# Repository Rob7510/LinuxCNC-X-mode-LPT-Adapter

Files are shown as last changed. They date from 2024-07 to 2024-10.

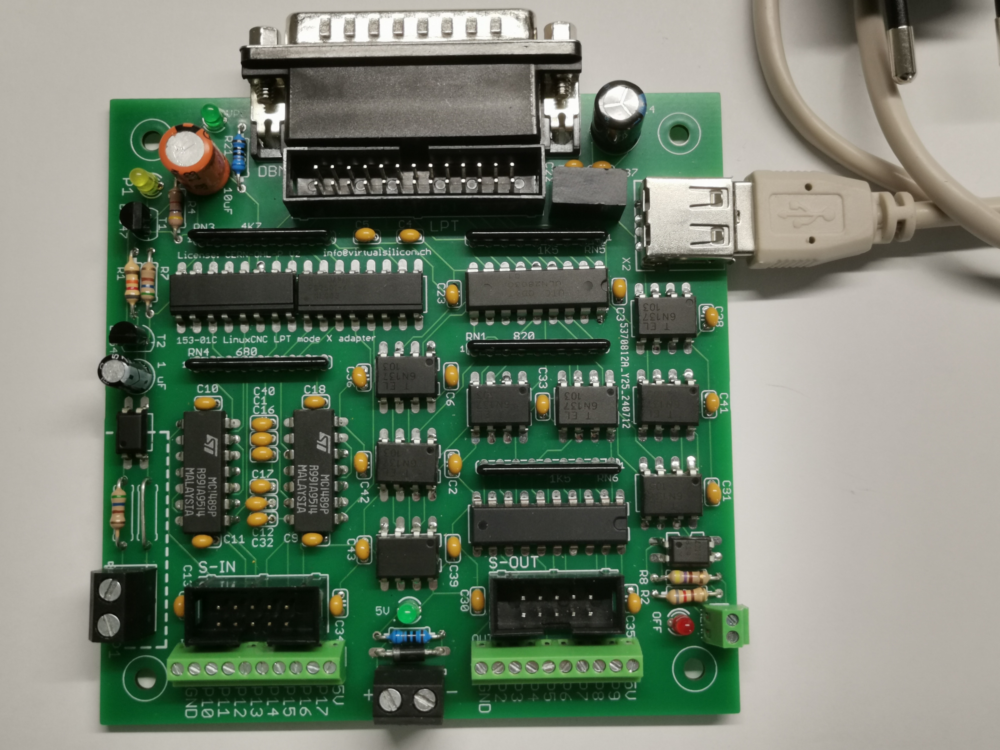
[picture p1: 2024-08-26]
153-01C LPT-X mode adapter prototype.jpg

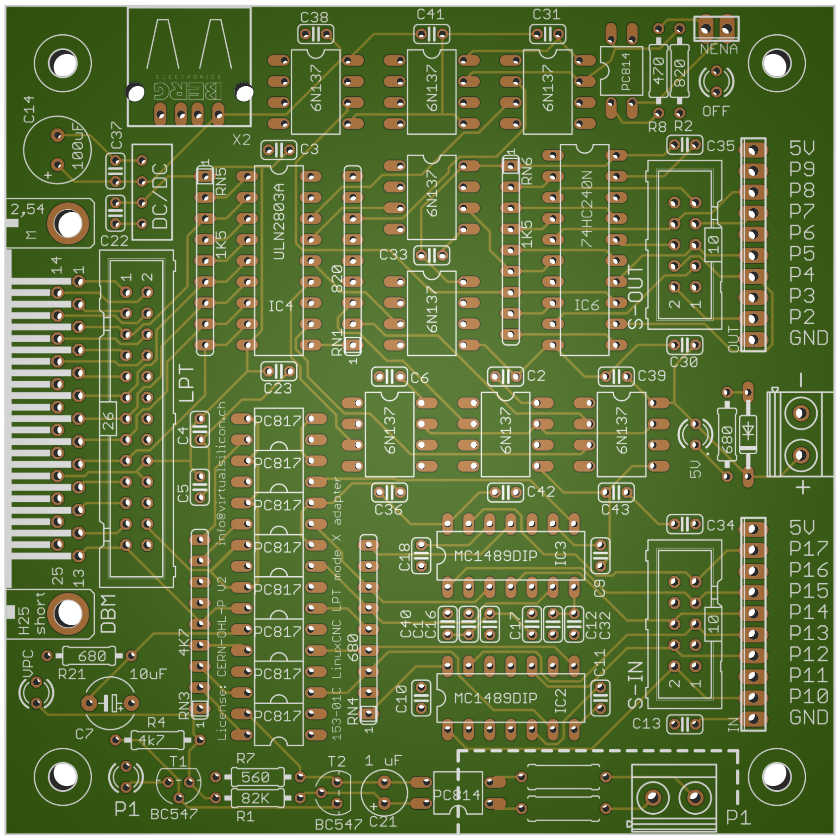
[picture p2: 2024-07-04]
153-01C image.png

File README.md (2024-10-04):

# LinuxCNC signal adapter for a parallel port operating in X-mode.
**Version 153-01C**

Many PC printer port option boards can be operated in 'X' mode in **LinuxCNC**, by setting this mode in the 'loadrt hal_parport' command.
In X-mode the 25-pin I/O connector provides 9 input ports (Pin 1, Pin 10-17) and 8 output ports (Pin 2 - Pin 9). This is usually sufficient for a small CNC. (I do not know if other software than LinuxCNC can set a Printer port card in X-mode).

The signal breakout for an X-mode adapter can be home built with a low cost dual layer PCB, with full electric isolation from the connected PC. This document provides the Eagle design and the Gerber manufacturing files for such a Breakout Board (BoB). The board size is kept to 10 x 10 cm to keep the manufacturing costs low (with Far-East PCB services). The **CERN-OHL-P V2** OpenHardware license applies, hence you are free to copy the design, modify it and sell/use the result.

**Design:**

  * The BoB input and output ports are electrically separated from the PC using optical couplers. The PC side of the circuit is powered via a small 5V isolated DC/DC converter. Te board uses approximately 150 mA, and can be powered with an old USB-A power adapter.
  * The board can be directly plugged into a 25 pin PC printer port, or connected via a standard 26 wire ribbon cable with a printer port connector on the other end. The 26 pin connector can also be used to plug in a signal monitor.
  * The Inputs for Pins 10 through 17 support a wide range of input signals (<u>+</u> 30V). The Pin 1 Input is fully isolated from the whole board, and can handle up to 300V AC or DC signals, for instance to check presence of the mains voltage or Power supply output.

**Inputs:**

**Pin 1** requires one or two series resistors (for DC) or capacitors (for AC) so that the current through the bipolar optocoupler (PC814) is in the range of 4 - 10 mA:
* For standard 5V signals use a 680 Ohm resistor. For voltages over 100V use two components in series.
* For DC voltages make sure the power dissipation in the resistor(s) does not exceed their rating.
* For 230V mains voltage use 2 x 150nF (400V) in series. To keep high voltages away from the board, mount the capacitors or resistors at the source, and fill the two onboard slots with jumpers.
* The P1 LED lights up when it detects a valid signal.

**Pins 10 - 17** are set to about 0V (False) for an input between -30 and + 0.5 V, and to 5V (True) for an input between 1.5 an 30V. These inputs suppress high frequency (>5KHz) pulses. The 10 pin ribbon connector connects Pin 10 - 17, as well as GND and 5V to a remote input panel.

**Outputs:**

**Pins 2 - 9 ** drive 5V signals with a current up to 35 mA. The fast optical couplers (6N137) can handle pulses as short as 2 microseconds. The 10 pin ribbon connector is for connection to a remote breakout panel. All outputs (typically used for stepper signals) can be collectively turned off with a logic input signal.

**Power supply:**

The USB connector on the BoB should be connected to an separate 5V USB power supply to maintain electric isolation from the PC. The onboard 2-pin 5V connector can be used to supply other 5V hardware like relay boards. If PC isolation is not needed, the BoB can be connected to one of the PC USB plugs, and the DC/DC converter can be replaced by two wires.

**Software:** XPtest-0.hal and xptest-0.xml provide a display of the X-mode adapter I/O ports and check / set their status. The test assumes that the BoB connects to the first printer port that the PC discovers.

**Assembly:**

The X-mode adapter 153-01C uses through-hole components to facilitate home assembly. The component list (BOM) has the details.
The small capacitors (useful values between 10 and 100 nF) are required to suppress RF disturbance.
The antiparallel diode next to the power connector will prevent damage in case the 5V is connected with the wrong polarity (I hate replacing dead chips).

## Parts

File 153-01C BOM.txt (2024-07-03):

Stückliste exportiert aus /home/robert/Project_data/Projects/153 LinuxCNC adapters/153-01C Mode X LPT adapter.sch am 03/07/2024 21:08

Part     Value     Device          Package         Description                           MF MPN          OC_FARNELL OC_NEWARK
.                  LED3MM          LED3MM          LED                                                                       
5V                 MKDSN1,5/2-5,08 MKDSN1,5/2-5,08 MKDSN 1,5/ 2-5,08 Printklemme                                             
AC/DC-IN           MKDSN1,5/2-5,08 MKDSN1,5/2-5,08 MKDSN 1,5/ 2-5,08 Printklemme                                             
C1                 C-EU025-024X044 C025-024X044    CAPACITOR, European symbol                                                
C2                 C-EU025-024X044 C025-024X044    CAPACITOR, European symbol                                                
C3                 C-EU025-024X044 C025-024X044    CAPACITOR, European symbol                                                
C4                 C-EU025-024X044 C025-024X044    CAPACITOR, European symbol                                                
C5                 C-EU025-024X044 C025-024X044    CAPACITOR, European symbol                                                
C6                 C-EU025-024X044 C025-024X044    CAPACITOR, European symbol                                                
C7       10uF      CPOL-EUE5-6     E5-6            POLARIZED CAPACITOR, European symbol                                      
C9                 C-EU025-024X044 C025-024X044    CAPACITOR, European symbol                                                
C10                C-EU025-024X044 C025-024X044    CAPACITOR, European symbol                                                
C11                C-EU025-024X044 C025-024X044    CAPACITOR, European symbol                                                
C12                C-EU025-024X044 C025-024X044    CAPACITOR, European symbol                                                
C13                C-EU025-024X044 C025-024X044    CAPACITOR, European symbol                                                
C14      100uF     CPOL-EUE3.5-8   E3,5-8          POLARIZED CAPACITOR, European symbol                                      
C16                C-EU025-024X044 C025-024X044    CAPACITOR, European symbol                                                
C17                C-EU025-024X044 C025-024X044    CAPACITOR, European symbol                                                
C18                C-EU025-024X044 C025-024X044    CAPACITOR, European symbol                                                
C21      1 uF      CPOL-EUE2.5-6   E2,5-6          POLARIZED CAPACITOR, European symbol                                      
C22                C-EU025-024X044 C025-024X044    CAPACITOR, European symbol                                                
C23                C-EU025-024X044 C025-024X044    CAPACITOR, European symbol                                                
C30                C-EU025-024X044 C025-024X044    CAPACITOR, European symbol                                                
C31                C-EU025-024X044 C025-024X044    CAPACITOR, European symbol                                                
C32                C-EU025-024X044 C025-024X044    CAPACITOR, European symbol                                                
C33                C-EU025-024X044 C025-024X044    CAPACITOR, European symbol                                                
C34                C-EU025-024X044 C025-024X044    CAPACITOR, European symbol                                                
C35                C-EU025-024X044 C025-024X044    CAPACITOR, European symbol                                                
C36                C-EU025-024X044 C025-024X044    CAPACITOR, European symbol                                                
C37                C-EU025-024X044 C025-024X044    CAPACITOR, European symbol                                                
C38                C-EU025-024X044 C025-024X044    CAPACITOR, European symbol                                                
C39                C-EU025-024X044 C025-024X044    CAPACITOR, European symbol                                                
C40                C-EU025-024X044 C025-024X044    CAPACITOR, European symbol                                                
C41                C-EU025-024X044 C025-024X044    CAPACITOR, European symbol                                                
C42                C-EU025-024X044 C025-024X044    CAPACITOR, European symbol                                                
C43                C-EU025-024X044 C025-024X044    CAPACITOR, European symbol                                                
D1                 1N4148DO35-10   DO35-10         DIODE                                                                     
DBM                M25HP           M25HP           SUB-D                                                 unknown    unknown  
DC/DC              VA-1205S        4SIL            DC DC Converter Single Output, 1 Watt                 unknown    unknown  
IC2      MC1489DIP MC1489DIP       DIL14           MC1489 quad line receiver DIP14                                           
IC3      MC1489DIP MC1489DIP       DIL14           MC1489 quad line receiver DIP14                                           
IC4      ULN2803A  ULN2803A        DIL18           DRIVER ARRAY                                                              
IC6      74HC240N  74HC240N        DIL20           Octal BUFFER and LINE DRIVER, 3-state                                     
IN                 MPT10           10POL254        PHOENIX CONNECTOR                                     unknown    unknown  
LPT                ML26            ML26            HARTING                                               unknown    unknown  
NENA               MPT2            2POL254         PHOENIX CONNECTOR                                     unknown    unknown  
OFF                LED3MM          LED3MM          LED                                                                       
OK-SIG   PC814     PC814           DIL04           SHARP OPTO COUPLER                                    9707662    unknown  
OK-SIG1  PC814     PC814           DIL04           SHARP OPTO COUPLER                                    9707662    unknown  
OK10     PC817     PC817           DIL04           SHARP OPTO COUPLER                       PC817X4J000F 9707727    97K7059  
OK11     PC817     PC817           DIL04           SHARP OPTO COUPLER                       PC817X4J000F 9707727    97K7059  
OK12     PC817     PC817           DIL04           SHARP OPTO COUPLER                       PC817X4J000F 9707727    97K7059  
OK13     PC817     PC817           DIL04           SHARP OPTO COUPLER                       PC817X4J000F 9707727    97K7059  
OK14     PC817     PC817           DIL04           SHARP OPTO COUPLER                       PC817X4J000F 9707727    97K7059  
OK15     PC817     PC817           DIL04           SHARP OPTO COUPLER                       PC817X4J000F 9707727    97K7059  
OK16     PC817     PC817           DIL04           SHARP OPTO COUPLER                       PC817X4J000F 9707727    97K7059  
OK17     PC817     PC817           DIL04           SHARP OPTO COUPLER                       PC817X4J000F 9707727    97K7059  
OKP2     6N137     6N137           DIL08           MOTOROLA OPTO COUPLER                    6N137        1328376    52M1895  
OKP3     6N137     6N137           DIL08           MOTOROLA OPTO COUPLER                    6N137        1328376    52M1895  
OKP4     6N137     6N137           DIL08           MOTOROLA OPTO COUPLER                    6N137        1328376    52M1895  
OKP5     6N137     6N137           DIL08           MOTOROLA OPTO COUPLER                    6N137        1328376    52M1895  
OKP6     6N137     6N137           DIL08           MOTOROLA OPTO COUPLER                    6N137        1328376    52M1895  
OKP7     6N137     6N137           DIL08           MOTOROLA OPTO COUPLER                    6N137        1328376    52M1895  
OKP8     6N137     6N137           DIL08           MOTOROLA OPTO COUPLER                    6N137        1328376    52M1895  
OKP9     6N137     6N137           DIL08           MOTOROLA OPTO COUPLER                    6N137        1328376    52M1895  
OUT                MPT10           10POL254        PHOENIX CONNECTOR                                     unknown    unknown  
P1                 LED3MM          LED3MM          LED                                                                       
R/C1               R-EU_0309/10    0309/10         RESISTOR, European symbol                                                 
R/C2               R-EU_0309/10    0309/10         RESISTOR, European symbol                                                 
R1       82K       R-EU_0207/10    0207/10         RESISTOR, European symbol                                                 
R2       820       R-EU_0207/10    0207/10         RESISTOR, European symbol                                                 
R4       4k7       R-EU_0207/10    0207/10         RESISTOR, European symbol                                                 
R7       560       R-EU_0207/10    0207/10         RESISTOR, European symbol                                                 
R8       470       R-EU_0207/10    0207/10         RESISTOR, European symbol                                                 
R21      680       R-EU_0207/10    0207/10         RESISTOR, European symbol                                                 
R36      680       R-EU_0207/10    0207/10         RESISTOR, European symbol                                                 
RN1      820       GE08R           SIL9            SIL RESISTOR                                          unknown    unknown  
RN3      4K7       GE08R           SIL9            SIL RESISTOR                                          unknown    unknown  
RN4      680       GE08R           SIL9            SIL RESISTOR                                          unknown    unknown  
RN5      1K5       GE08R           SIL9            SIL RESISTOR                                          unknown    unknown  
RN6      1K5       GE08R           SIL9            SIL RESISTOR                                          unknown    unknown  
S-IN               ML10            ML10            HARTING                                               unknown    unknown  
S-OUT              ML10            ML10            HARTING                                               unknown    unknown  
T1       BC547     BC547           TO92            NPN TRANSISTOR                                                            
T2       BC547     BC547           TO92            NPN TRANSISTOR                                                            
VPC                LED3MM          LED3MM          LED                                                                       
X2                 PN87520         PN87520         BERG USB connector                                    unknown    unknown

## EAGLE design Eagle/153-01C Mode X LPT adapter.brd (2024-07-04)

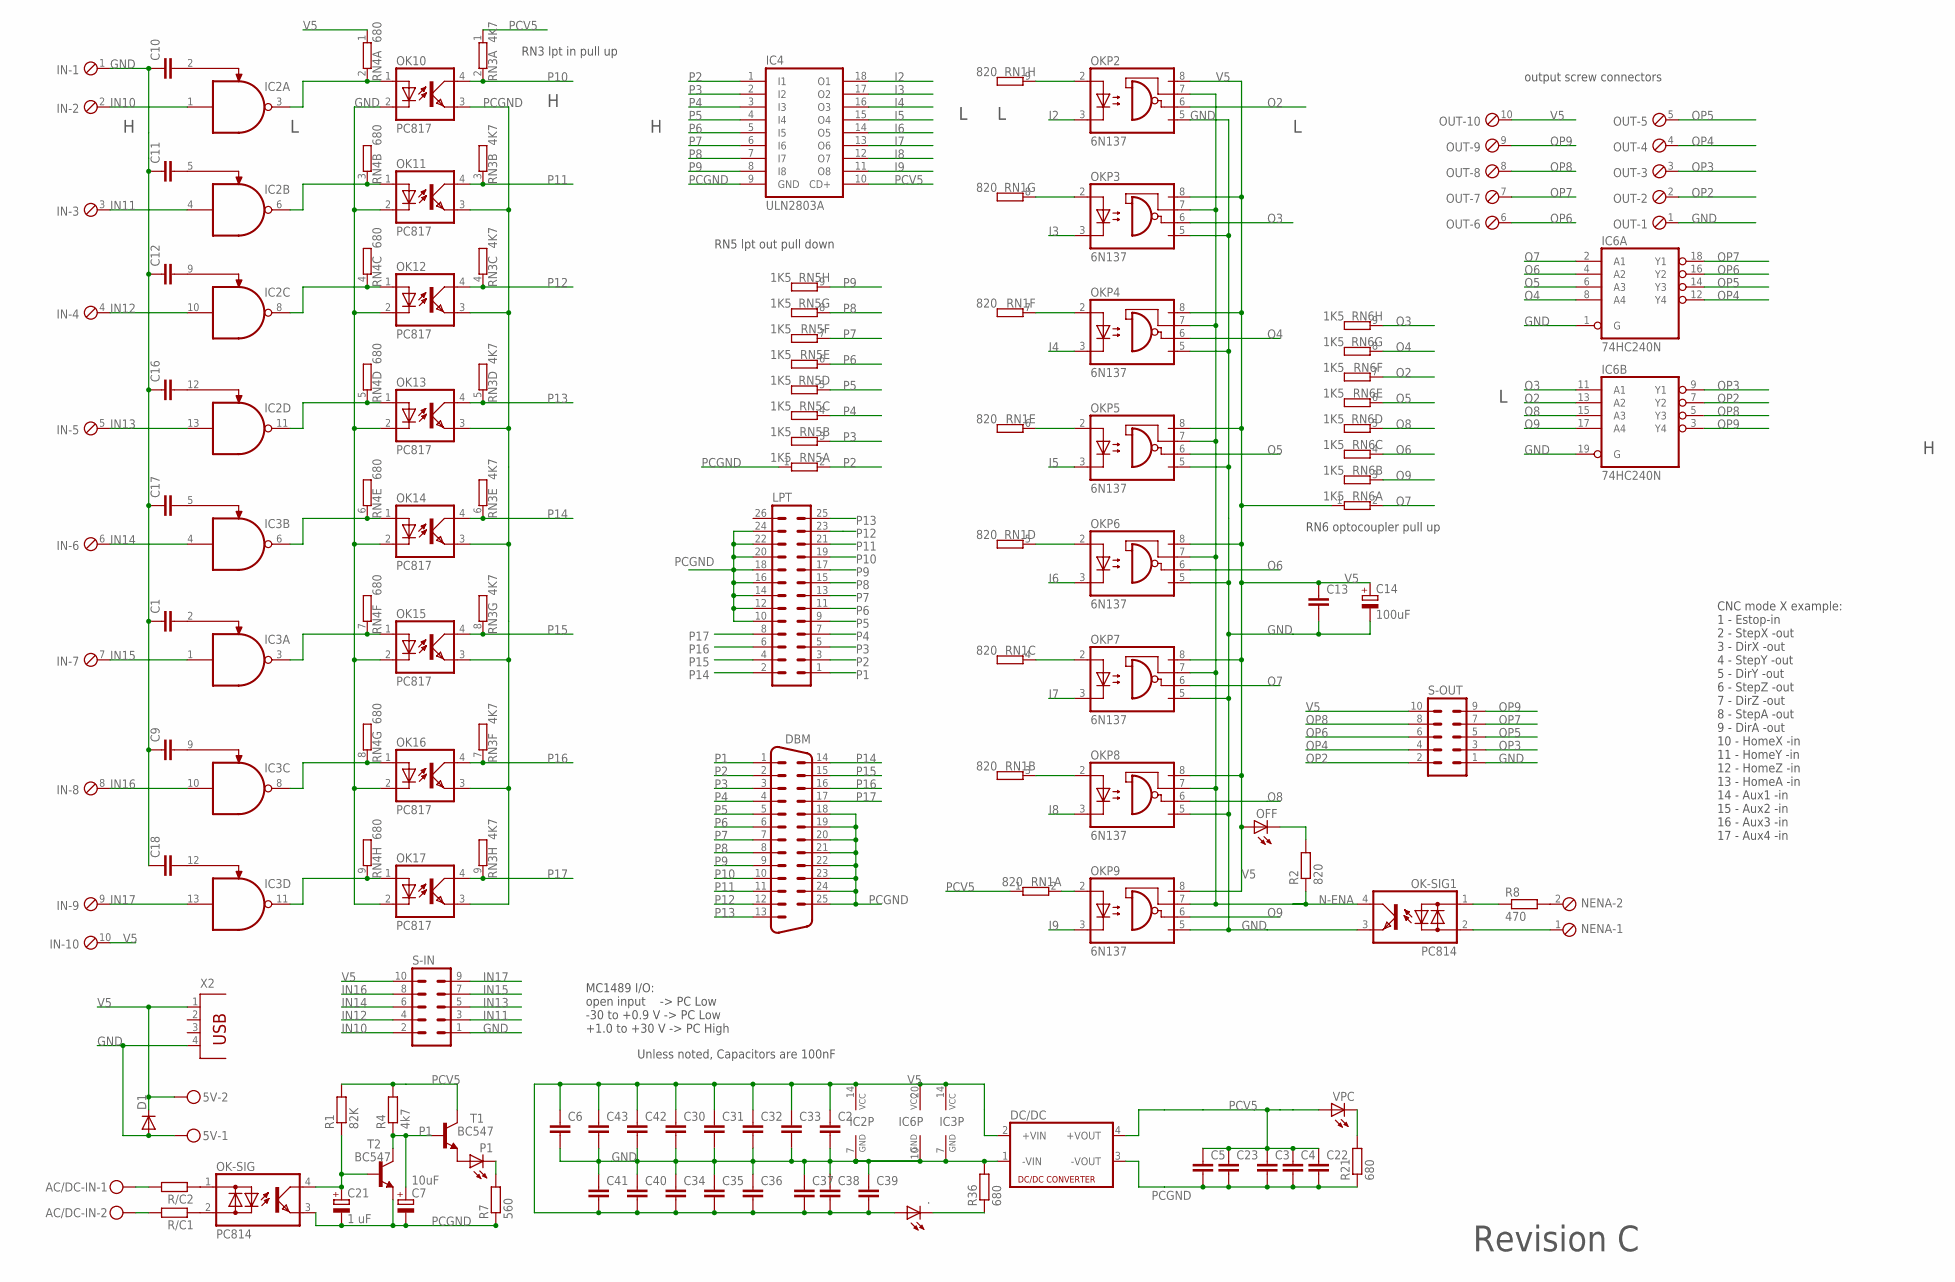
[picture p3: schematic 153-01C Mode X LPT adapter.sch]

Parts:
5V: MKDSN1,5/2-5,08
.: LED3MM
AC/DC-IN: MKDSN1,5/2-5,08
C1, C2, C3, C4, C5, C6, C9, C10, C11, C12, C13, C16, C17, C18, C22, C23, C30, C31, C32, C33, C34, C35, C36, C37, C38, C39, C40, C41, C42, C43: C-EU025-024X044; C025-024X044
C7: 10uF; E5-6
C14: 100uF; E3,5-8
C21: 1 uF; E2,5-6
D1: 1N4148DO35-10; DO35-10
DBM: M25HP
DC/DC: VA-1205S; 4SIL
IC2, IC3: MC1489DIP; DIL14
IC4: ULN2803A; DIL18
IC6: 74HC240N; DIL20
IN: MPT10; 10POL254
LPT: ML26
NENA: MPT2; 2POL254
OFF: LED3MM
OK10, OK11, OK12, OK13, OK14, OK15, OK16, OK17: PC817; DIL04
OK-SIG, OK-SIG1: PC814; DIL04
OKP2, OKP3, OKP4, OKP5, OKP6, OKP7, OKP8, OKP9: 6N137; DIL08
OUT: MPT10; 10POL254
P1: LED3MM
R1: 82K; 0207/10
R2: 820; 0207/10
R4: 4k7; 0207/10
R7: 560; 0207/10
R8: 470; 0207/10
R21, R36: 680; 0207/10
R/C1, R/C2: R-EU_0309/10; 0309/10
RN1: 820; SIL9
RN3: 4K7; SIL9
RN4: 680; SIL9
RN5, RN6: 1K5; SIL9
S-IN: ML10
S-OUT: ML10
T1, T2: BC547; TO92
VPC: LED3MM
X2: PN87520

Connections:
GND: 5V.1, C1.1, C2.2, C6.2, C9.1, C10.1, C11.1, C12.1, C13.2, C14.-, C16.1, C17.1, C18.1, C30.2, C31.2, C32.2, C33.2, C34.1, C35.1, C36.1, C37.1, C38.1, C39.1, C40.1, C41.1, C42.2, C43.2, D1.A, DC/DC.1 (-VIN), IC2.7 (GND), IC3.7 (GND), IC6.1 (G), IC6.10 (GND), IC6.19 (G), IN.1, OK10.2 (C), OK11.2 (C), OK12.2 (C), OK13.2 (C), OK14.2 (C), OK15.2 (C), OK16.2 (C), OK17.2 (C), OK-SIG1.3 (E), OKP2.5 (GND), OKP3.5 (GND), OKP4.5 (GND), OKP5.5 (GND), OKP6.5 (GND), OKP7.5 (GND), OKP8.5 (GND), OKP9.5 (GND), OUT.1, R36.2, S-IN.1, S-OUT.1, X2.4
I2: IC4.18 (O1), OKP2.3 (C)
I3: IC4.17 (O2), OKP3.3 (C)
I4: IC4.16 (O3), OKP4.3 (C)
I5: IC4.15 (O4), OKP5.3 (C)
I6: IC4.14 (O5), OKP6.3 (C)
I7: IC4.13 (O6), OKP7.3 (C)
I8: IC4.12 (O7), OKP8.3 (C)
I9: IC4.11 (O8), OKP9.3 (C)
IN10: IC2.1 (I0), IN.2, S-IN.2
IN11: IC2.4 (I0), IN.3, S-IN.3
IN12: IC2.10 (I0), IN.4, S-IN.4
IN13: IC2.13 (I0), IN.5, S-IN.5
IN14: IC3.4 (I0), IN.6, S-IN.6
IN15: IC3.1 (I0), IN.7, S-IN.7
IN16: IC3.10 (I0), IN.8, S-IN.8
IN17: IC3.13 (I0), IN.9, S-IN.9
unnamed: OKP6.2 (A), RN1.5 (2)
unnamed: OKP9.2 (A), RN1.2
unnamed: C10.2, IC2.2 (I1)
unnamed: R21.2, VPC.K (C)
unnamed: C17.2, IC3.5 (I1)
unnamed: OFF.K (C), R2.2
unnamed: IC2.6 (O), OK11.1 (A), RN4.3 (2)
unnamed: IC2.8 (O), OK12.1 (A), RN4.4 (2)
unnamed: C1.2, IC3.2 (I1)
unnamed: C9.2, IC3.9 (I1)
unnamed: C18.2, IC3.12 (I1)
unnamed: IC2.3 (O), OK10.1 (A), RN4.2
unnamed: IC2.11 (O), OK13.1 (A), RN4.5 (2)
unnamed: IC3.6 (O), OK14.1 (A), RN4.6 (2)
unnamed: IC3.3 (O), OK15.1 (A), RN4.7 (2)
unnamed: IC3.8 (O), OK16.1 (A), RN4.8 (2)
unnamed: OK-SIG.1 (AC1), R/C2.1
unnamed: OK-SIG.2 (AC2), R/C1.1
unnamed: IC3.11 (O), OK17.1 (A), RN4.9 (2)
unnamed: AC/DC-IN.2, R/C1.2
unnamed: AC/DC-IN.1, R/C2.2
unnamed: OKP7.2 (A), RN1.4 (2)
unnamed: OKP8.2 (A), RN1.3 (2)
unnamed: C21.+, OK-SIG.4 (C), R1.1, T2.2 (B)
unnamed: ..K (C), R36.1
unnamed: C11.2, IC2.5 (I1)
unnamed: C12.2, IC2.9 (I1)
unnamed: C16.2, IC2.12 (I1)
unnamed: OKP5.2 (A), RN1.6 (2)
unnamed: OKP4.2 (A), RN1.7 (2)
unnamed: OK-SIG1.1 (AC1), R8.1
unnamed: OKP3.2 (A), RN1.8 (2)
unnamed: OKP2.2 (A), RN1.9 (2)
unnamed: P1.K (C), R7.2
unnamed: P1.A, T1.1 (E)
unnamed: NENA.2, R8.2
unnamed: NENA.1, OK-SIG1.2 (AC2)
N-ENA: OK-SIG1.4 (C), OKP2.7 (VE), OKP3.7 (VE), OKP4.7 (VE), OKP5.7 (VE), OKP6.7 (VE), OKP7.7 (VE), OKP8.7 (VE), OKP9.7 (VE), R2.1
O2: IC6.13 (A2), OKP2.6 (VO), RN6.7 (2)
O3: IC6.11 (A1), OKP3.6 (VO), RN6.9 (2)
O4: IC6.8 (A4), OKP4.6 (VO), RN6.8 (2)
O5: IC6.6 (A3), OKP5.6 (VO), RN6.6 (2)
O6: IC6.4 (A2), OKP6.6 (VO), RN6.4 (2)
O7: IC6.2 (A1), OKP7.6 (VO), RN6.2
O8: IC6.15 (A3), OKP8.6 (VO), RN6.5 (2)
O9: IC6.17 (A4), OKP9.6 (VO), RN6.3 (2)
OP2: IC6.7 (Y2), OUT.2, S-OUT.2
OP3: IC6.9 (Y1), OUT.3, S-OUT.3
OP4: IC6.12 (Y4), OUT.4, S-OUT.4
OP5: IC6.14 (Y3), OUT.5, S-OUT.5
OP6: IC6.16 (Y2), OUT.6, S-OUT.6
OP7: IC6.18 (Y1), OUT.7, S-OUT.7
OP8: IC6.5 (Y3), OUT.8, S-OUT.8
OP9: IC6.3 (Y4), OUT.9, S-OUT.9
P1: C7.+, DBM.1, LPT.1, R4.1, T1.2 (B), T2.3 (C)
P2: DBM.2, IC4.1 (I1), LPT.3, RN5.2
P3: DBM.3, IC4.2 (I2), LPT.5, RN5.3 (2)
P4: DBM.4, IC4.3 (I3), LPT.7, RN5.4 (2)
P5: DBM.5, IC4.4 (I4), LPT.9, RN5.5 (2)
P6: DBM.6, IC4.5 (I5), LPT.11, RN5.6 (2)
P7: DBM.7, IC4.6 (I6), LPT.13, RN5.7 (2)
P8: DBM.8, IC4.7 (I7), LPT.15, RN5.8 (2)
P9: DBM.9, IC4.8 (I8), LPT.17, RN5.9 (2)
P10: DBM.10, LPT.19, OK10.4 (COL), RN3.2
P11: DBM.11, LPT.21, OK11.4 (COL), RN3.3 (2)
P12: DBM.12, LPT.23, OK12.4 (COL), RN3.4 (2)
P13: DBM.13, LPT.25, OK13.4 (COL), RN3.5 (2)
P14: DBM.14, LPT.2, OK14.4 (COL), RN3.6 (2)
P15: DBM.15, LPT.4, OK15.4 (COL), RN3.8 (2)
P16: DBM.16, LPT.6, OK16.4 (COL), RN3.7 (2)
P17: DBM.17, LPT.8, OK17.4 (COL), RN3.9 (2)
PCGND: C3.2, C4.2, C5.2, C7.-, C21.-, C22.2, C23.2, DBM.18, DBM.19, DBM.20, DBM.21, DBM.22, DBM.23, DBM.24, DBM.25, DC/DC.3 (-VOUT), IC4.9 (GND), LPT.10, LPT.12, LPT.14, LPT.16, LPT.18, LPT.20, LPT.22, LPT.24, OK10.3 (EMIT), OK11.3 (EMIT), OK12.3 (EMIT), OK13.3 (EMIT), OK14.3 (EMIT), OK15.3 (EMIT), OK16.3 (EMIT), OK17.3 (EMIT), OK-SIG.3 (E), R7.1, R21.1, RN5.1, T2.1 (E)
PCV5: C3.1, C4.1, C5.1, C22.1, C23.1, DC/DC.4 (+VOUT), IC4.10 (CD+), R1.2, R4.2, RN1.1, RN3.1, T1.3 (C), VPC.A
V5: 5V.2, ..A, C2.1, C6.1, C13.1, C14.+, C30.1, C31.1, C32.1, C33.1, C34.2, C35.2, C36.2, C37.2, C38.2, C39.2, C40.2, C41.2, C42.1, C43.1, D1.C, DC/DC.2 (+VIN), IC2.14 (VCC), IC3.14 (VCC), IC6.20 (VCC), IN.10, OFF.A, OKP2.8 (VCC), OKP3.8 (VCC), OKP4.8 (VCC), OKP5.8 (VCC), OKP6.8 (VCC), OKP7.8 (VCC), OKP8.8 (VCC), OKP9.8 (VCC), OUT.10, RN4.1, RN6.1, S-IN.10, S-OUT.10, X2.1

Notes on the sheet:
CNC mode X example: 1 - Estop-in 2 - StepX -out 3 - DirX -out 4 - StepY -out 5 - DirY -out 6 - StepZ -out 7 - DirZ -out 8 - StepA -out 9 - DirA -out 10 - HomeX -in 11 - HomeY -in 12 - HomeZ -in 13 - HomeA -in 14 - Aux1 -in 15 - Aux2 -in 16 - Aux3 -in 17 - Aux4 -in
MC1489 I/O: open input -> PC Low -30 to +0.9 V -> PC Low +1.0 to +30 V -> PC High
RN5 lpt out pull down
RN3 lpt in pull up
RN6 optocoupler pull up
output screw connectors
Unless noted, Capacitors are 100nF
Revision C

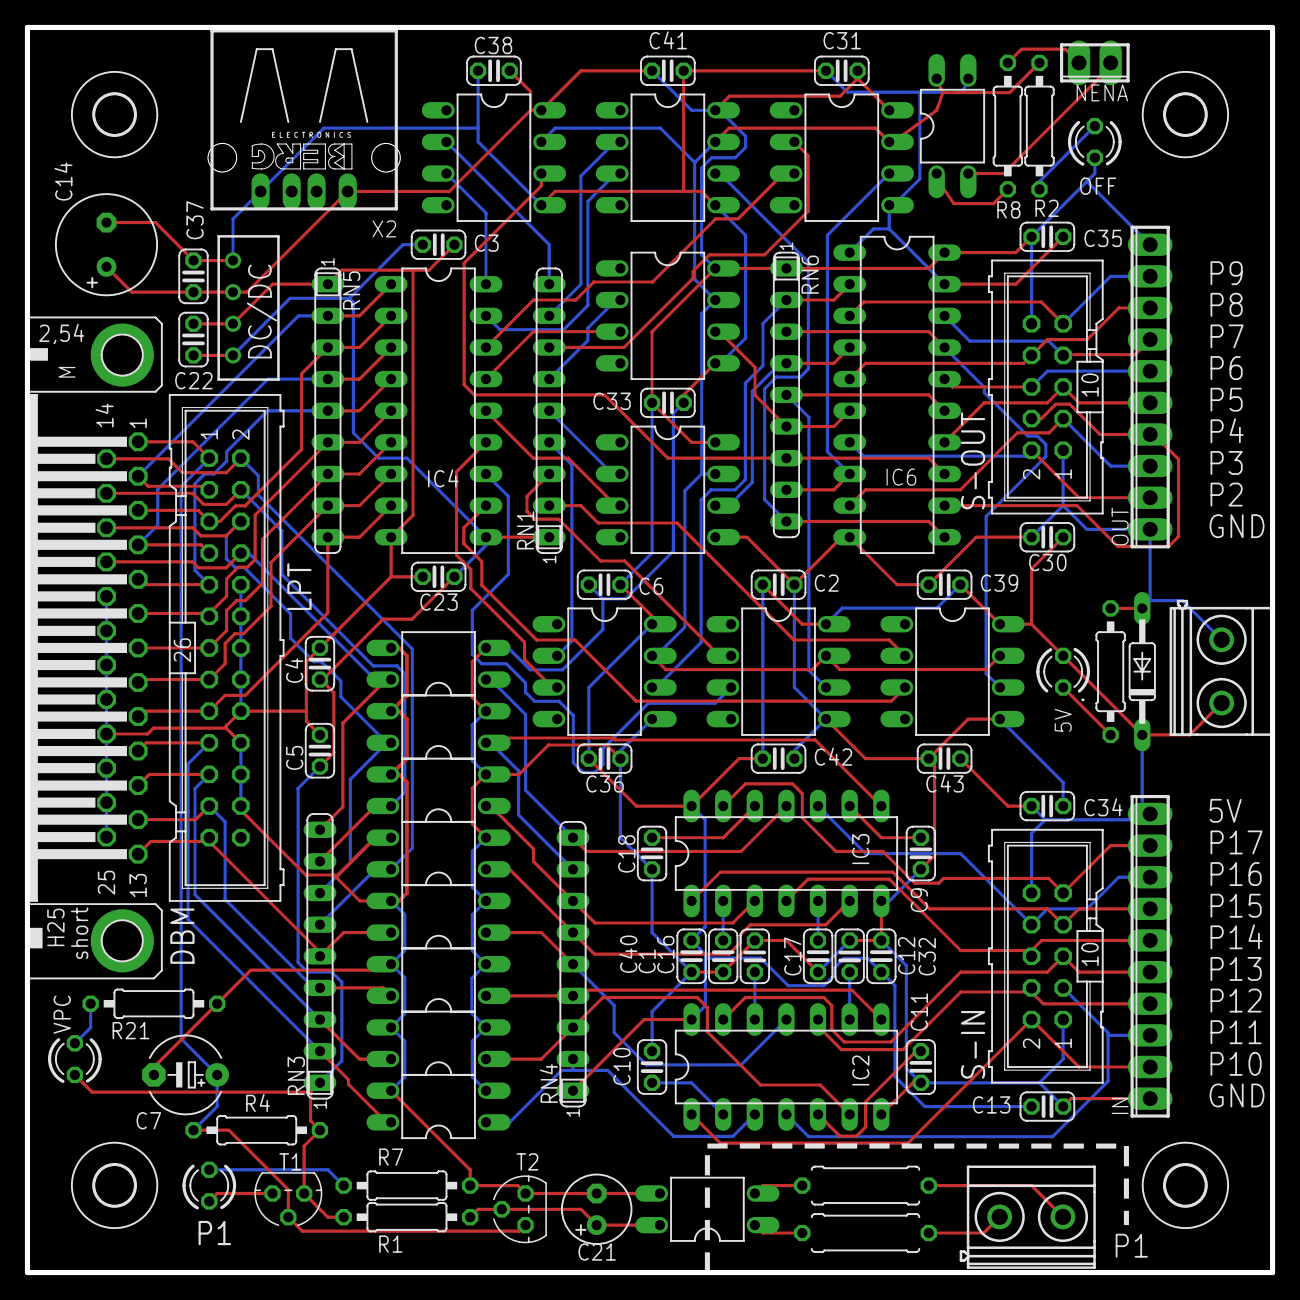
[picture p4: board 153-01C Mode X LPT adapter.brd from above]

Board: 2 copper layers, 100.0 x 100.0 mm, 91 parts (0 on the bottom side), 91 nets.

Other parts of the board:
U$1, U$2, U$3, U$4: 3,2

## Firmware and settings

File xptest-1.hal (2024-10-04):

loadrt hal_parport cfg="1 x"
loadusr -Wn PortTest pyvcp -c PortTest xptest-1.xml
loadrt threads name1=porttest period1=1000000
addf parport.1.read porttest
addf parport.1.write porttest

# OUTPUTS

net pin02 PortTest.btn02 parport.1.pin-02-out PortTest.led-02
net pin03 PortTest.btn03 parport.1.pin-03-out PortTest.led-03
net pin04 PortTest.btn04 parport.1.pin-04-out PortTest.led-04
net pin05 PortTest.btn05 parport.1.pin-05-out PortTest.led-05
net pin06 PortTest.btn06 parport.1.pin-06-out PortTest.led-06
net pin07 PortTest.btn07 parport.1.pin-07-out PortTest.led-07
net pin08 PortTest.btn08 parport.1.pin-08-out PortTest.led-08
net pin09 PortTest.btn09 parport.1.pin-09-out PortTest.led-09

# INPUT

net pin01 parport.1.pin-01-in PortTest.led-01
net pin10 parport.1.pin-10-in PortTest.led-10
net pin11 parport.1.pin-11-in PortTest.led-11
net pin12 parport.1.pin-12-in PortTest.led-12
net pin13 parport.1.pin-13-in PortTest.led-13
net pin14 parport.1.pin-14-in PortTest.led-14
net pin15 parport.1.pin-15-in PortTest.led-15
net pin16 parport.1.pin-16-in PortTest.led-16
net pin17 parport.1.pin-17-in PortTest.led-17

start

# loadusr halmeter

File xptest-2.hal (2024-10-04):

loadrt hal_parport cfg="2 x"
loadusr -Wn PortTest pyvcp -c PortTest xptest-2.xml
loadrt threads name1=porttest period1=1000000
addf parport.2.read porttest
addf parport.2.write porttest

# OUTPUTS

net pin02 PortTest.btn02 parport.2.pin-02-out PortTest.led-02
net pin03 PortTest.btn03 parport.2.pin-03-out PortTest.led-03
net pin04 PortTest.btn04 parport.2.pin-04-out PortTest.led-04
net pin05 PortTest.btn05 parport.2.pin-05-out PortTest.led-05
net pin06 PortTest.btn06 parport.2.pin-06-out PortTest.led-06
net pin07 PortTest.btn07 parport.2.pin-07-out PortTest.led-07
net pin08 PortTest.btn08 parport.2.pin-08-out PortTest.led-08
net pin09 PortTest.btn09 parport.2.pin-09-out PortTest.led-09

# INPUT

net pin01 parport.2.pin-01-in PortTest.led-01
net pin10 parport.2.pin-10-in PortTest.led-10
net pin11 parport.2.pin-11-in PortTest.led-11
net pin12 parport.2.pin-12-in PortTest.led-12
net pin13 parport.2.pin-13-in PortTest.led-13
net pin14 parport.2.pin-14-in PortTest.led-14
net pin15 parport.2.pin-15-in PortTest.led-15
net pin16 parport.2.pin-16-in PortTest.led-16
net pin17 parport.2.pin-17-in PortTest.led-17

start

# loadusr halmeter

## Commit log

2024-07-04 Got the initial list back Remove deleted files from repository
    [153-01C Mode X LPT adapter.brd, 153-01C Mode X LPT adapter.dsn, 153-01C Mode X LPT adapter.sch]
2024-07-04 New upload, removed the DSN file
    [153-01C Mode X LPT adapter.brd, 153-01C Mode X LPT adapter.sch]
2024-07-04 Update of text ofn the PCB top layer
    [153-01C Mode X LPT adapter.brd]
2024-07-05 updated top silkscreen, created Eagle and Gerber directory
    [153-01C Mode X LPT adapter.brd, 153-01C Mode X LPT adapter.sch]
2024-07-05 Added the 2 direvctories
    [153-01C Mode X LPT adapter.brd, 153-01C Mode X LPT adapter.sch]
2024-07-09 added tests...
    [xptest-0.hal]
2024-10-04 updated tests and brd image
    [xptest-0.hal, xptest-1.hal, xptest-2.hal]

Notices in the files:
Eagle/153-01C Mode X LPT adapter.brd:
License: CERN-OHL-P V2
